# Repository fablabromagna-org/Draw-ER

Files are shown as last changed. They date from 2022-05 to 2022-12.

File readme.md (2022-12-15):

# Draw-ER
### da un'idea originale di [MakersBox](https://www.instructables.com/Arduino-Drawing-Robot/)
Un piccolo, lento ma economico robot disegnatore, autocostruibile da tutti e programmabile in Python per insegnare il coding in modo divertente.

# Eccolo
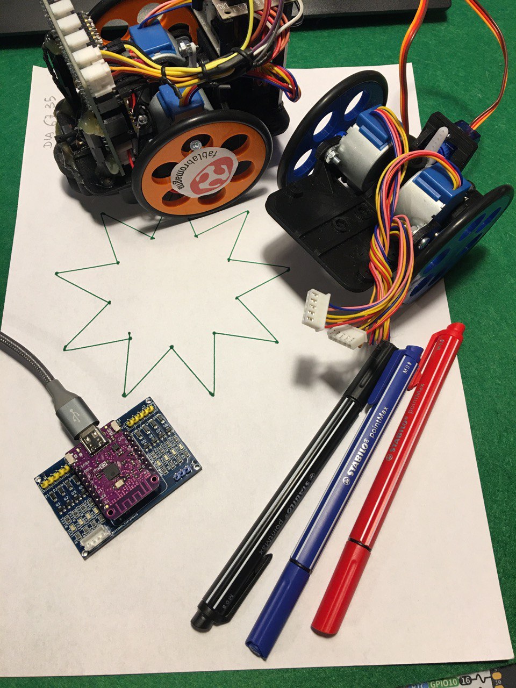
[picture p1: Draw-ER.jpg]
Draw-ER


## stampa la locandina da tenere in classe
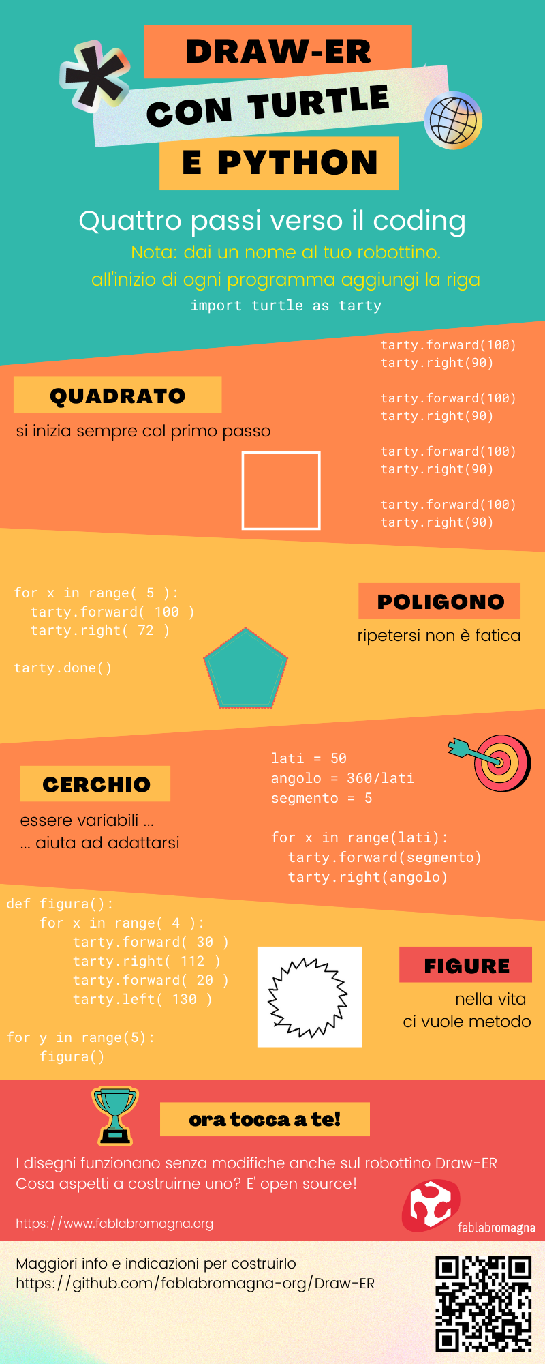
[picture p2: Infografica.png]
Locandina


## istruzioni per il montaggio

<a href="https://cutt.ly/montaggio-Draw-ER">link al documento GDocs</a>

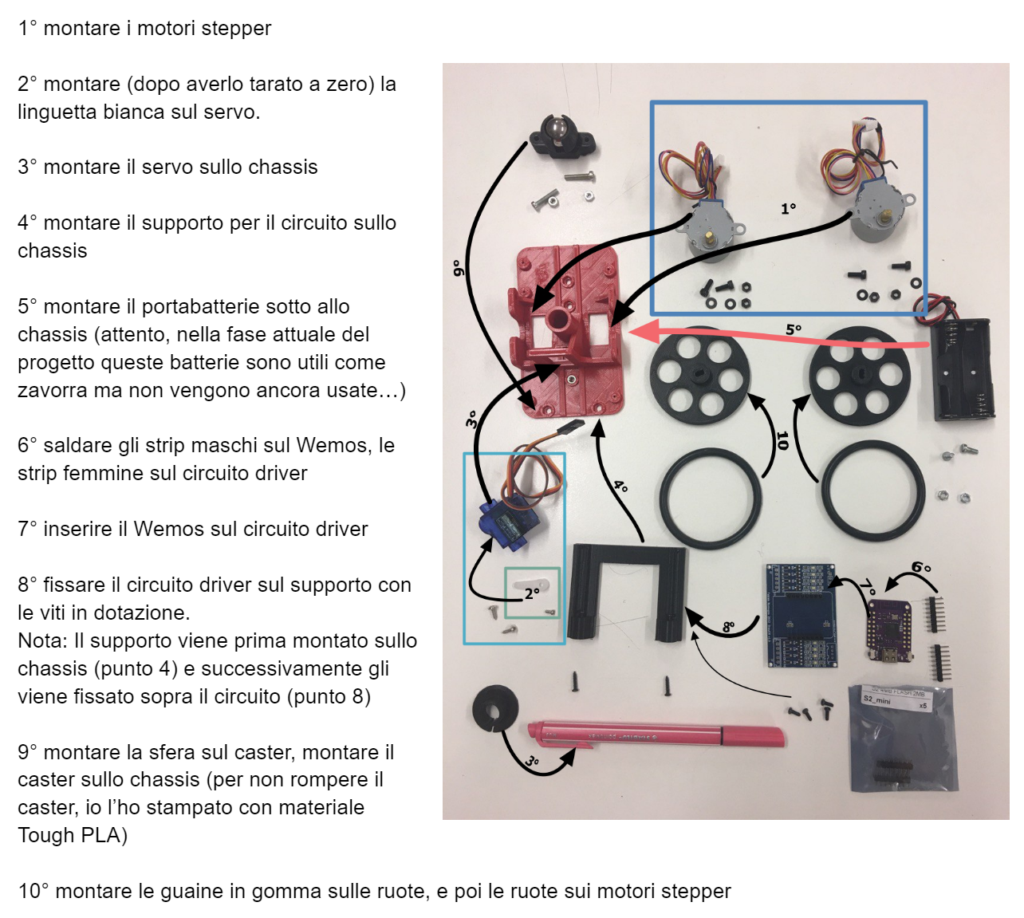
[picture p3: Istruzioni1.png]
Istruzioni


#### Ci serve un fornitore per queste viti... ci date una mano?
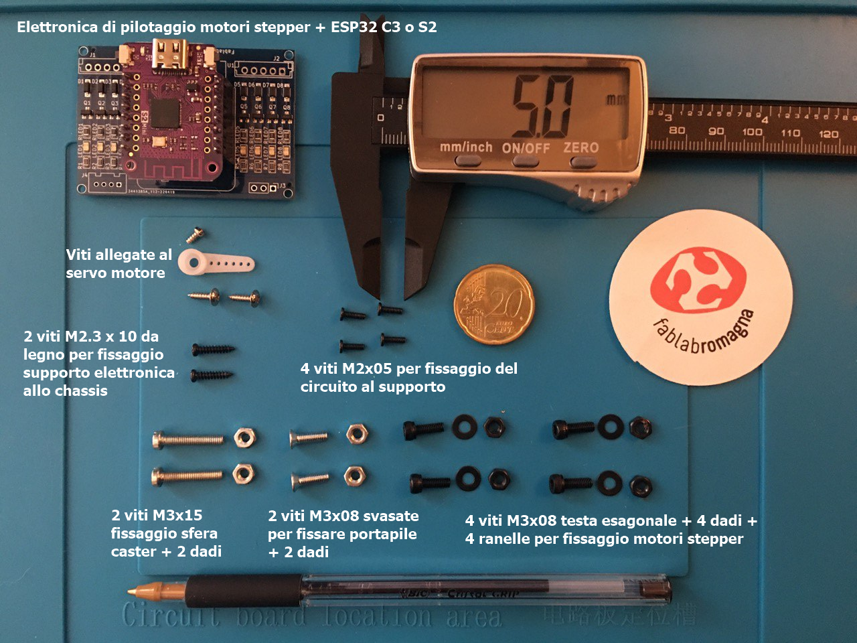
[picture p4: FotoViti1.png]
Viti


#### questa foto è utile per capire come sono montati i connettori
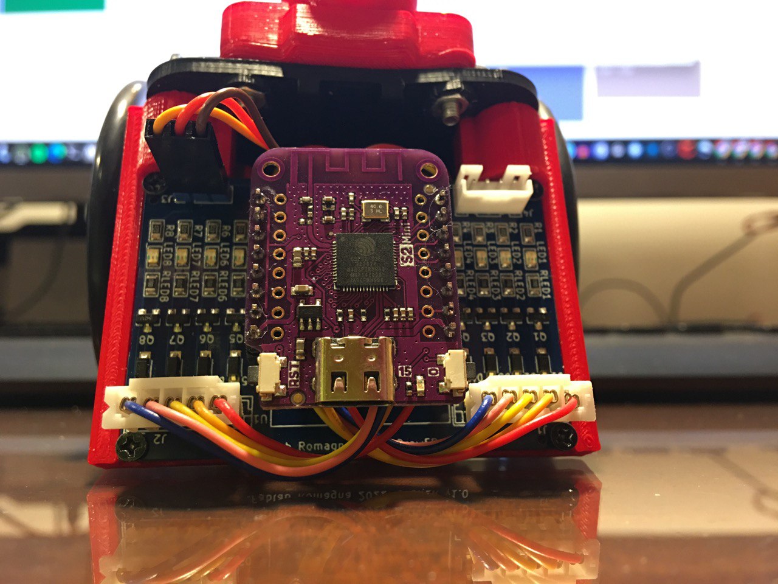
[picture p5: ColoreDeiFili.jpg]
Colore dei fili


## usa Kicad per modificare lo schema e il PCB

<a href="https://github.com/fablabromagna-org/Draw-ER/tree/master/File%20Kicad">Kicad</a>

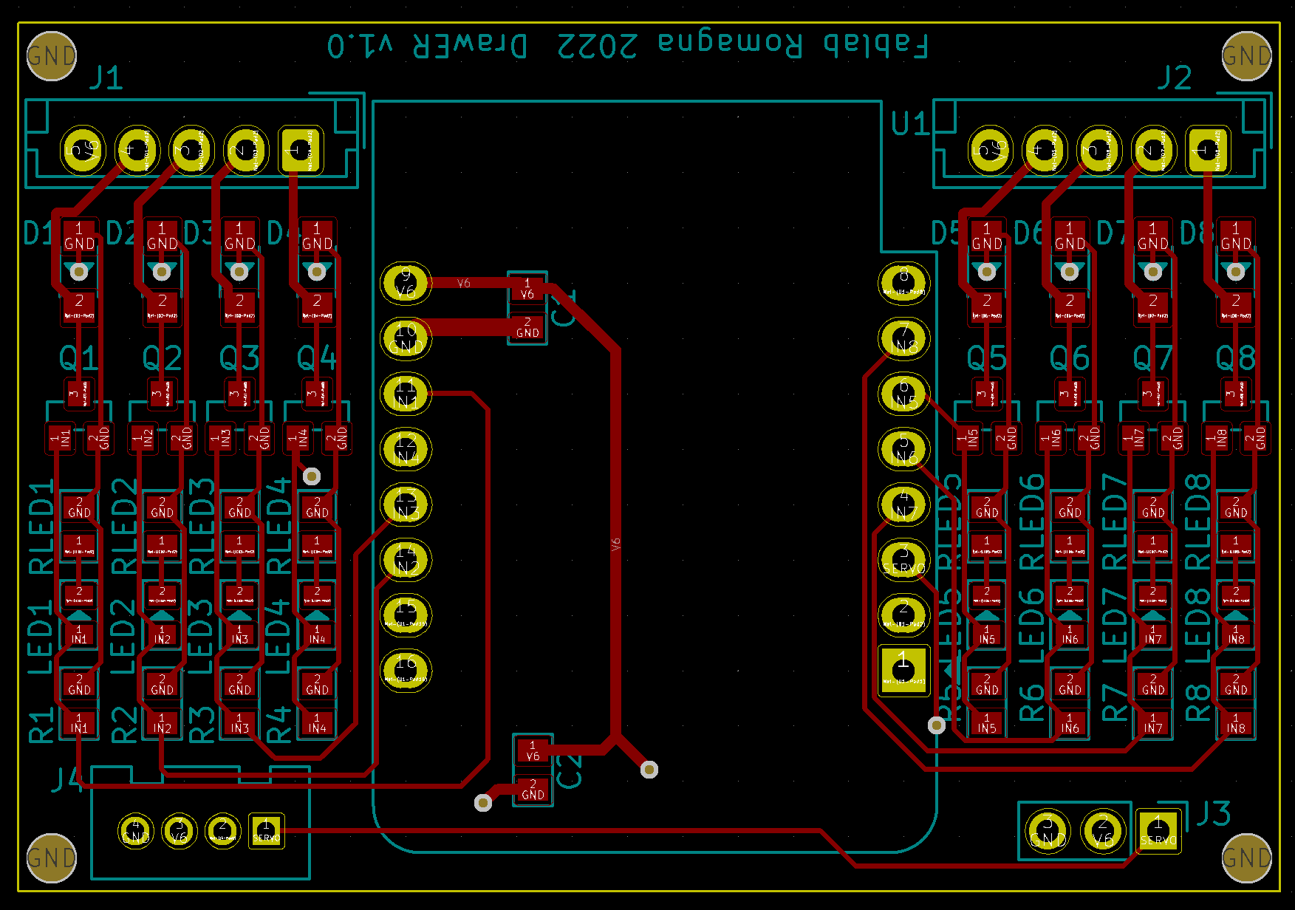
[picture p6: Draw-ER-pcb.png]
PCB


## dai un'occhiata allo schema
<a href="Schematic.pdf">Download PDF</a>

## dai un'occhiata anche al lavoro di Alessandro Capanna Kappa! che sta cercando in tutti i modi di togliere il filo!! :-)
https://github.com/1Kappa1/Draw-Er.utility.file

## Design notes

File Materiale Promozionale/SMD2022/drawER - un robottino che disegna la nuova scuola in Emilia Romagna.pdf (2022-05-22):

25/03/22, 17:28 | drawER - un robottino che disegna la nuova scuola in Emilia Romagna

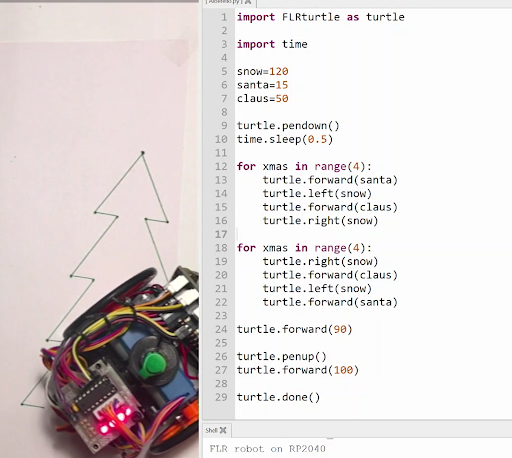
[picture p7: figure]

www.schoolmakerday.it/registrazione/candidatura/viewespol?id=a_491 | 1/3

Home registrazioni (/registrazione) (http://www.schoolmakerday.it/registrazione)
/ drawER - un robottino che disegna la nuova scuola in Emilia Romagna

Modifica (/registrazione/candidatura/espolupdate?id=a_491) (http://www.schoolmakerday.it/registrazione/candidatura/espolupdate?id=a_491)

# drawER - un robottino che disegna la nuova scuola in Emilia Romagna

Abbiamo realizzato un robottino per lo studio della geometria computazionale e del pensiero computazionale, usabile nelle scuole di primo grado ma realizzabile dai ragazzi e dalle ragazze delle superiori, per promuovere la collaborazione tra vari livelli e ordini di scuola.

Un'idea in parte ancora un po' sulla carta ma con un prototipo quasi funzionante in fase di sviluppo in due classi terze ITTS in ambito PCTO.
I progetti saranno pubblicati su github.com

# Chi siamo

## FabLab Romagna makerspace presso l'ITTS "Belluzzi - da Vinci"

Fablab

www.schoolmakerday.it/registrazione/candidatura/viewespol?id=a_491 | 2/3

Referente: Maurizio Conti

Presentazione del team da compilare

Sito web: (/registrazione/candidatura/viewespol?id=a_491) (http://www.schoolmakerday.it/registrazione/candidatura/viewespol?id=a_491)

Temi:
ambito Maker
Robotica
Stampa 3D
STEM
ambito Agenda2030
Istruzione di qualità
Parità di genere
ambito Azioni PNSD
Scenari innovativi per lo sviluppo di competenze digitali applicate
Portare il pensiero logico-computazionale a tutta la scuola primaria Aggiornare il curricolo di “Tecnologia” alla scuola secondaria di primo grado

# Ulteriori dati:

Dichiarazione liberatoria: si
Richiesta trasporto: si
Data di richiesta trasporto: 2022-03-25 17:25:49 Numero di partecipanti: 60
Torna all'elenco (/registrazione/candidatura/candidature) (http://www.schoolmakerday.it/registrazione/candidatura/candidature)

www.schoolmakerday.it/registrazione/candidatura/viewespol?id=a_491 | 3/3

© IIS Belluzzi-Fioravanti (http://www.belluzzifioravanti.it) / Servizio Marconi TSI USR-ER (http://serviziomarconi.w.istruzioneer.it/) 2016-2022. Powered by Yii Framework (http://www.yiiframework.com/). - Note relative a Privacy e Cookie (http://www.schoolmakerday.it/privacy-e-cookie/)

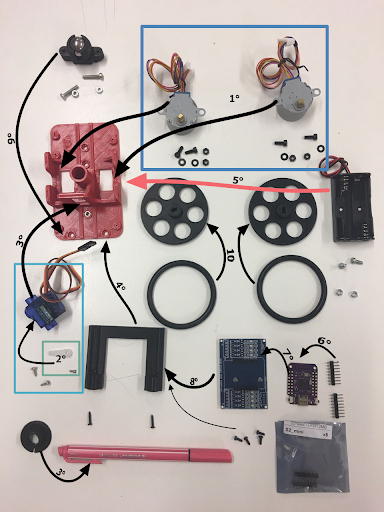
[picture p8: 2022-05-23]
Componenti.png

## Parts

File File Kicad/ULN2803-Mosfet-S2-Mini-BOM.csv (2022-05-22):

Comment | Designator | Footprint | LCSC
CERAMIC-10UF-10V-10%-X7R_0805_ | C1,C2 | OPL_Capacitor:C0805 | C126586
SMD-DIODE-SCHOTTKY-20V-1A_SOD-123_ | D1,D2,D3,D4,D5,D6,D7,D8 | OPL_Discrete:SOD-123 | C84354
Step Motor | J1,J2 | Connector_JST:JST_EH_B5B-EH-A_1x05_P2.50mm_Vertical
Conn_01x03_Male | J3 | Connector_PinHeader_2.54mm:PinHeader_1x03_P2.54mm_Vertical
GROVE-CONNECTOR-DIP_4P-2.0_ | J4 | OPL_Connector:HW4-2.0
SMD-LED-CLEAR-RED_0805_ | LED1,LED2,LED3,LED4,LED5,LED6,LED7,LED8 | OPL_Opto:LED-0805 | C2764885
SMD-MOSFET-N-CH-20V-2.1A-CJ2302_SOT-23_ | Q1,Q2,Q3,Q4,Q5,Q6,Q7,Q8 | OPL_Discrete:SOT-23 | C91104
SMD-RES-4.7K-5%-1_8W_0805_ | R1,R2,R3,R4,R5,R6,R7,R8 | OPL_Resistor:R0805 | C473295
SMD-RES-220R-5%-1_8W_0805_ | RLED1,RLED2,RLED3,RLED4,RLED5,RLED6,RLED7,RLED8 | OPL_Resistor:R0805 | C365277
WeMos_D1_mini | U1 | Module:WEMOS_D1_mini_light

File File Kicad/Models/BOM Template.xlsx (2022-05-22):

Designator | Manufacturer Part Number or Seeed SKU | Qty | Link
C1,C2,C3,C4,C5 | RHA0J471MCN1GS | 5 | https://www.digikey.com.cn/product-detail/zh/nichicon/RHA0J471MCN1GS/493-3771-1-ND/2209480
A1,A4 | RH0111-30002 | 2 | https://statics3.seeedstudio.com/images/opl/datasheet/318020010.pdf
D1 | CYBLE-014008-00 | 1 | https://www.digikey.com.cn/product-detail/zh/cypress-semiconductor-corp/CYBLE-014008-00/428-3600-1-ND/6052585

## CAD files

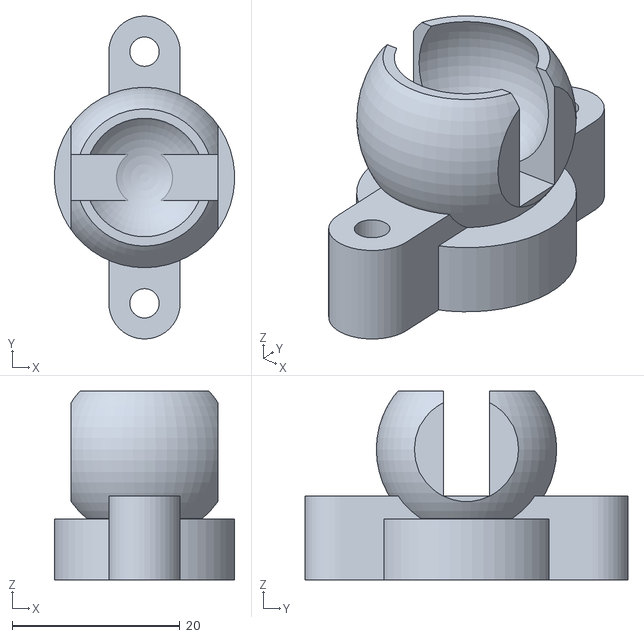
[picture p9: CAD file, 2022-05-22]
Cad3D/FLRCaster/FLRCaster.stl
21.5 x 38.5 x 22.5

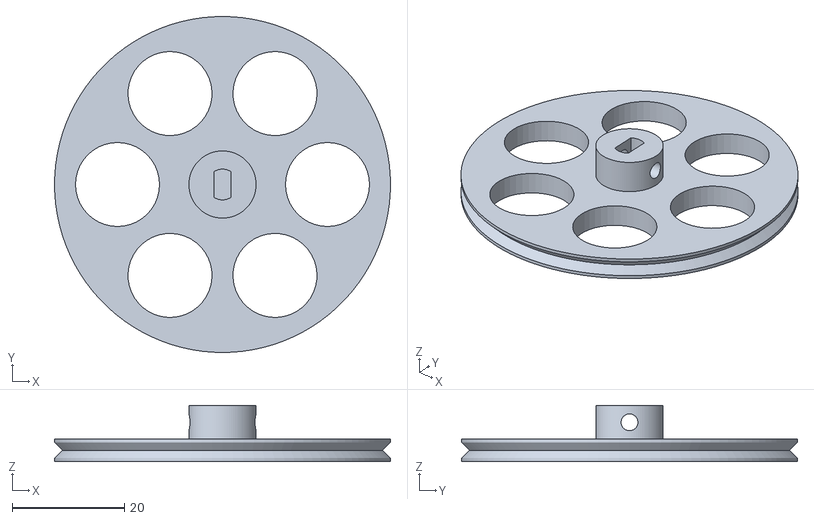
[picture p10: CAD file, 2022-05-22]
Cad3D/STL per SMD22/60mm_wheel_spoked.stl
60.0 x 60.0 x 10.0

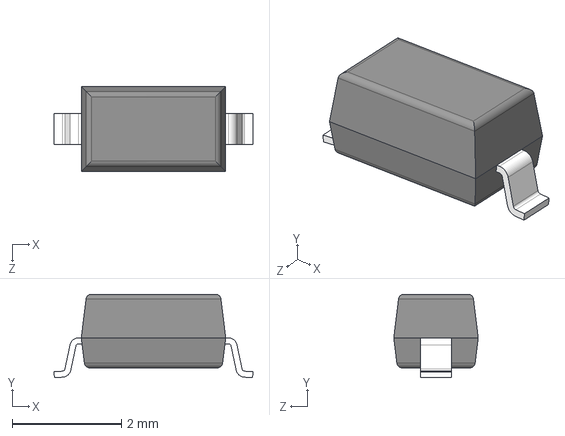
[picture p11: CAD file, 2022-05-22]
File Kicad/Models/B5819W-TP.step
3.65 x 1.53 x 1.55 mm

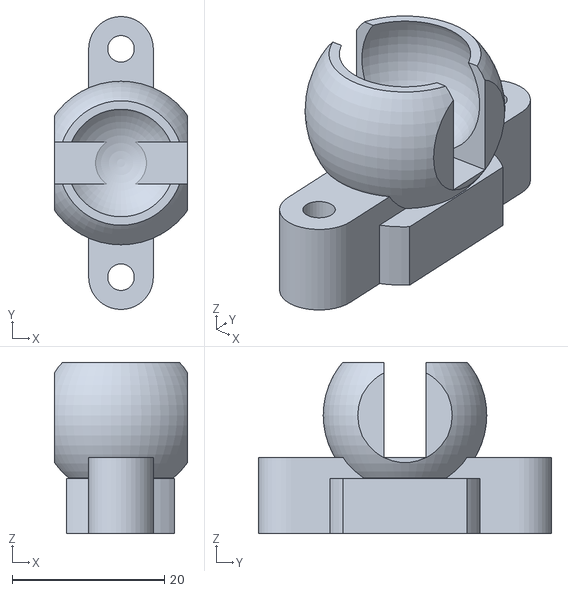
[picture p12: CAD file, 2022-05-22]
Cad3D/FLRCaster/FLRCaster V3 Smussato.stl
17.5 x 38.5 x 22.5

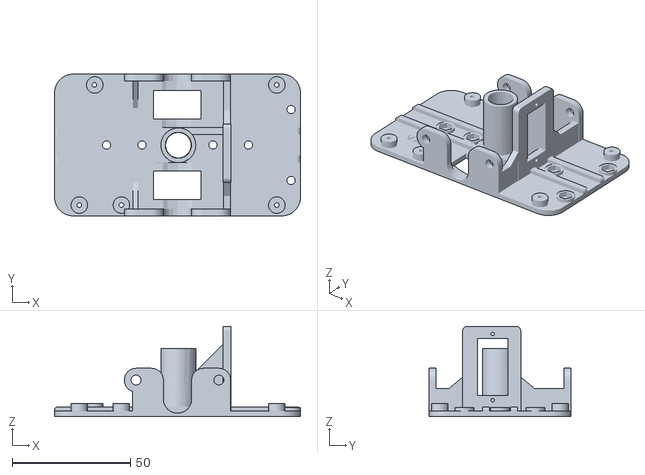
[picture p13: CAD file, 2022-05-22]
Cad3D/STL per SMD22/1x-Chassis v2.1.stl
104.0 x 60.0 x 38.3

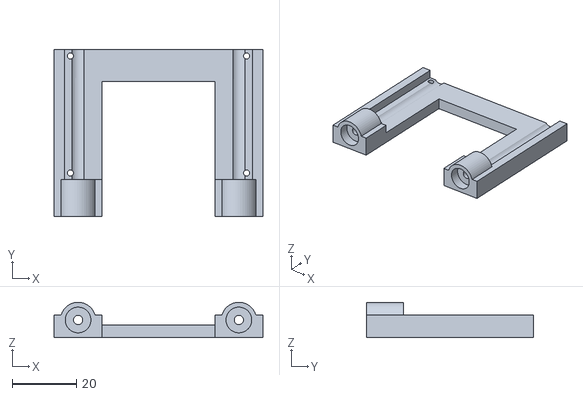
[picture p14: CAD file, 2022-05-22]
Cad3D/STL per SMD22/Supporto Wemos mini con fori.stl
65.0 x 52.0 x 11.0

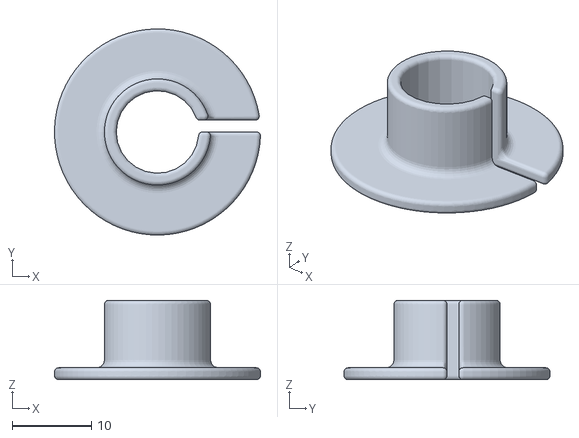
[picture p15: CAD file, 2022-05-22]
Cad3D/STL per SMD22/1xPenCollar10-4mm.stl
26.0 x 26.0 x 10.0

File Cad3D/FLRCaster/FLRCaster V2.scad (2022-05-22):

// Original: http://www.thingiverse.com/thing:8959/
// Marble Caster by HipsterLogic

// Modified by 648.ken@gmail.com
// MakersBox.blogspot.com

// Added tapper the top lip to keep it from snagging on things.
// Added recess for screw heads if baseThickness > 3mm
// Added pedistal base so you can adjust platform hieght.

// Modificato da maurizio.conti@ittsrimini.edu.it
// Alzata la quota di 7.3mm per portarlo alla pari dello chassis con ruote da 60mm



deckHeight = 18.5;    // from chassis bottom to ground, (must be at lease ballDiameter)
ballDiameter = 16.5;    // 7/16" ball bearing = 12.25mm, WAS 16.5  16mm = 5/8" ball bearing
ballTolerance = 0.25;  // play between ball and surface
wallThickness = 2.5;
gapWidth = ballDiameter / 3;
baseThickness = 10; // WAS 3
newQuota = 7.3;

//baseHeight = ballDiameter + wallThickness * 2;
pedistalWidth = ballDiameter + wallThickness * 2;

baseWidth = 30; // distance between mounting holes

M3holeDia = 3.5;
M3nutDia = 6.5;


echo(deckHeight);
baseHeight = deckHeight - ballDiameter / 2;
echo(baseHeight);

module mainShape(){

    // Alzata la quota di tutto l'assembly
    translate([0, 0, -newQuota]) {

        // mounting cross-piece
        translate([-baseWidth/2, -wallThickness - M3holeDia / 2, 0]) 
            cube([baseWidth, wallThickness * 2 + M3holeDia, baseThickness]);
        
        // bolt ends
        translate([baseWidth / 2, 0, 0]) 
            cylinder(baseThickness, M3holeDia / 2 + wallThickness, M3holeDia / 2 + wallThickness, $fn=40);
        translate([-baseWidth / 2, 0, 0]) 
            cylinder(baseThickness, M3holeDia / 2 + wallThickness, M3holeDia / 2 + wallThickness, $fn=40);

        // main cylindrical body
        translate([0, 0, 0])
            cylinder(baseHeight - 3, pedistalWidth / 2, pedistalWidth / 2, $fn=50);
    }
    
    difference(){
        // tapper shere at top
        translate([0, 0, baseHeight - 2])
            sphere(pedistalWidth / 2, $fn=50);
                
        // shave the top flat
        translate([0, 0, baseHeight + ballDiameter / 2 - ballDiameter / 5])
            cylinder(25, 25, 25, $fn=50);
        
        // shave the bottom	flat	
        translate([0, 0, -12])
            cylinder(12, 25, 25, $fn=50);
  
    };
}

module cutout(){
    
    // ball hole
	translate([0, 0, baseHeight + ballTolerance]) 
        sphere(ballDiameter / 2 + ballTolerance, $fn=50);
	
    // slot to remove ball
    slotOffset = ballDiameter / 2.5;  // distance below baseHeight to cut slot
    if (baseHeight - slotOffset > baseThickness){
        translate([-gapWidth / 2, -baseWidth / 2, baseHeight - slotOffset]) 
            cube([gapWidth, baseWidth, ballDiameter]);
        
        }
    else{ // don't cut into base
        translate([-gapWidth / 2, -baseWidth / 2, baseThickness-newQuota]) 
            cube([gapWidth, baseWidth, ballDiameter]);        
    }
    
    //trim sides
    translate([-25, ballDiameter / 2 + 0.5, 0]) 
            cube([50, ballDiameter, 50]);      

    translate([-25, -ballDiameter - 0.5, 0]) 
            cube([50, ballDiameter / 2, 50]);    

    if ((baseHeight - ballDiameter / 2) > baseThickness){
         // ball void to save material
        translate([0, 0, baseHeight - ballDiameter - 1]) 
            sphere(ballDiameter / 2, $fn=50);
    }

}

module mountingHoles(){

    // left m3 hole
	translate([baseWidth / 2, 0, -baseThickness ])
        cylinder(baseThickness + 3, M3holeDia / 2, M3holeDia / 2, $fn=30);

    // countersink
	//translate([baseWidth / 2, 0, 2]) 
    //rotate([0, 0, 30])
	//cylinder(baseThickness + 2, M3holeDia, //M3holeDia, $fn=6);

    // right m3 hole
	translate([-baseWidth / 2, 0, -baseThickness]) 
        cylinder(baseThickness + 3, M3holeDia / 2, M3holeDia/2, $fn=30);

    // countersink
	//translate([-baseWidth / 2, 0, 2]) 
    //rotate([0, 0, 30])
    //cylinder(baseThickness + 2, M3holeDia, M3holeDia, $fn=6);
}

rotate([0, 0, 90])

difference(){
	mainShape();
	cutout();
	mountingHoles();
}

// show ball?
//translate([0, 0, baseHeight]) 
//    sphere(ballDiameter/2, $fn=50);

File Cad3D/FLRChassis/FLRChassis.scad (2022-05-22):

$fn = 64;

include <FLRModule.scad>


baseThickness = 2.4;
cornerRounding = 8;
plateOffset = 0;    // shift entire plate on x axis
railOffset = 16;     // plate lenght - railLength
M3holeDia = 3.5;
M3nutDia = 6.5;
holeOffset = M3holeDia * 1.2;
batteryOffset = 15;
casterFromEdge = 4;   // from edge to CL of caster bolt holes
cassis_wid = 75; // 94 for full Raspberry Pi, 84 for A+ ?
cassis_len = 140;


penDiameter = 15.0;
penRadius = penDiameter / 2;
baseLen = 34.5;
baseWid = 20;

railWidth = 2;

cutout_len = 45;
cutout_wid = 15;

trinketX = -41.5;
trinketY = -50.8/2;
sensor_offset = 13;



difference(){
    
    union(){
        // cassis plate
        translate([-cassis_len / 2 - plateOffset, -cassis_wid / 2, 0])
        roundedCube(cassis_len, cassis_wid, baseThickness, cornerRounding);
        

        // rails
        rail_offset = 5.5;
        translate([-cassis_len / 2 - plateOffset, 
                   +rail_offset+railWidth, baseThickness / 2])
            rotate([90, 0, 0])    
            roundedCube(cassis_len/2-8, 3.0, railWidth, 1);

        translate([-cassis_len / 2 - plateOffset, 
                   - rail_offset, baseThickness / 2])
            rotate([90, 0, 0])    
            roundedCube(cassis_len/2-8, 3.0, railWidth, 1); 

        translate([8, 
                   - rail_offset+railWidth -2, baseThickness / 2])
            rotate([90, 0, 0])    
            roundedCube(cassis_len/2-8, 3.0, railWidth, 1);

        translate([8, 
                   + rail_offset +2, baseThickness / 2])
            rotate([90, 0, 0])    
            roundedCube(cassis_len/2-8, 3.0, railWidth, 1); 


        
        //battery standoffs
        translate([batteryOffset, 0, baseThickness - 1])
        cylinder(baseThickness, standoffDia + 1, standoffDia + 1);  
        translate([batteryOffset + 15, 0, baseThickness - 1])
        cylinder(baseThickness, standoffDia + 1, standoffDia + 1);
        //translate([batteryOffset + 30, 0, baseThickness - 1])
        //cylinder(baseThickness, d=standoffDia + 1, d=standoffDia + 1);   

        //translate([-batteryOffset, 0, baseThickness - 1])
        //cylinder(baseThickness, d=standoffDia + 1, d=standoffDia + 1);  
        translate([-batteryOffset - 0, 0, baseThickness - 1])
        cylinder(baseThickness, standoffDia + 1, standoffDia + 1);
        translate([-batteryOffset - 15, 0, baseThickness - 1])
        cylinder(baseThickness, standoffDia + 1, standoffDia + 1);        

        // caster standoffs
        translate([cassis_len / 2 - casterFromEdge - plateOffset, -15, baseThickness -1])
        cylinder(baseThickness, standoffDia + 1, standoffDia + 1);  
        translate([cassis_len / 2 - casterFromEdge - plateOffset, 15, baseThickness -1])
        cylinder(baseThickness, standoffDia + 1, standoffDia + 1); 

        // trinket standoffs
        translate([trinketX, trinketY, 0])
        cylinder(standoffThickness, standoffDia / 2, standoffDia / 2);
        
        translate([trinketX + 17.8, trinketY, 0])
        cylinder(standoffThickness, standoffDia / 2, standoffDia / 2);        

        translate([trinketX + 17.8, trinketY + 50.8, 0])
        cylinder(standoffThickness, standoffDia / 2, standoffDia / 2);

        translate([trinketX, trinketY + 50.8, 0])
        cylinder(standoffThickness, standoffDia / 2, standoffDia / 2);        

        // nose standoffs
        translate([cassis_len/2 - 14, trinketY, 0])
        cylinder(standoffThickness, standoffDia / 2, standoffDia / 2);

        translate([cassis_len/2 - 14, trinketY + 50.8, 0])
        cylinder(standoffThickness, standoffDia / 2, standoffDia / 2); 

        
    }

    // center pen hole
    cylinder(baseThickness * 2, penRadius, penRadius);

   
    // caster holes
    translate([cassis_len / 2 - casterFromEdge - plateOffset, -15, 0])
    cylinder(baseThickness*2, M3holeDia, M3holeDia);     
    translate([cassis_len / 2 - casterFromEdge - plateOffset, 15, 0])
    cylinder(baseThickness*2, M3holeDia, M3holeDia);    

    // caster nut nolders
    translate([cassis_len / 2 - casterFromEdge - plateOffset, -15, baseThickness - 1])
    cylinder(baseThickness, M3nutDia, M3nutDia, $fn=6);
    translate([cassis_len / 2 - casterFromEdge - plateOffset, 15, baseThickness - 1])
    cylinder(baseThickness, M3nutDia, M3nutDia, $fn=6);

 
    // battery holes
    translate([batteryOffset, 0, 0])
    cylinder(baseThickness, M3holeDia, M3holeDia);  
    translate([batteryOffset + 15, 0, 0])
    cylinder(baseThickness, M3holeDia, M3holeDia);
    
    translate([-batteryOffset - 0, 0, 0])
    cylinder(baseThickness, M3holeDia, M3holeDia);
    translate([-batteryOffset - 15, 0, 0])
    cylinder(baseThickness, M3holeDia, M3holeDia); 

    // battery nut nolders
    translate([batteryOffset, 0, baseThickness - 1])
    cylinder(baseThickness, M3nutDia, M3nutDia, $fn=6);
    translate([batteryOffset + 15, 0, baseThickness - 1])
    cylinder(baseThickness, M3nutDia, M3nutDia, $fn=6);

    translate([-batteryOffset - 0, 0, baseThickness - 1])
    cylinder(baseThickness, M3nutDia, M3nutDia, $fn=6);
    translate([-batteryOffset - 15, 0, baseThickness - 1])
    cylinder(baseThickness, M3nutDia, M3nutDia, $fn=6);

    // trinket holes
    translate([trinketX, trinketY, 0])
    cylinder(standoffThickness * 2, standoffHoleDia / 2, standoffHoleDia / 2);

    translate([trinketX + 17.8, trinketY, 0])
    cylinder(standoffThickness * 2, standoffHoleDia / 2, standoffHoleDia / 2);

    translate([trinketX, trinketY + 50.8, 0])
    cylinder(standoffThickness * 2, standoffHoleDia / 2, standoffHoleDia / 2);

    translate([trinketX + 17.8, trinketY + 50.8, 0])
    cylinder(standoffThickness * 2, standoffHoleDia / 2, standoffHoleDia / 2);

    // nose standoff holees
    translate([cassis_len/2-14, trinketY, 0])
    cylinder(standoffThickness * 2, standoffHoleDia / 2, standoffHoleDia / 2);

    translate([cassis_len/2 -14, trinketY + 50.8, 0])
    cylinder(standoffThickness * 2, standoffHoleDia / 2, standoffHoleDia / 2);

 
}


standoffDia = 7;
standoffThickness = 5.5;
standoffHoleDia = 2;

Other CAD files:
Cad3D/STL per SMD22/Ruota60 con foro allargato e nuts più piccole.stl
Cad3D/FLRCaster/FLRCaster V3 Smussato.scad
Cad3D/FLRChassis/FLRModule.scad

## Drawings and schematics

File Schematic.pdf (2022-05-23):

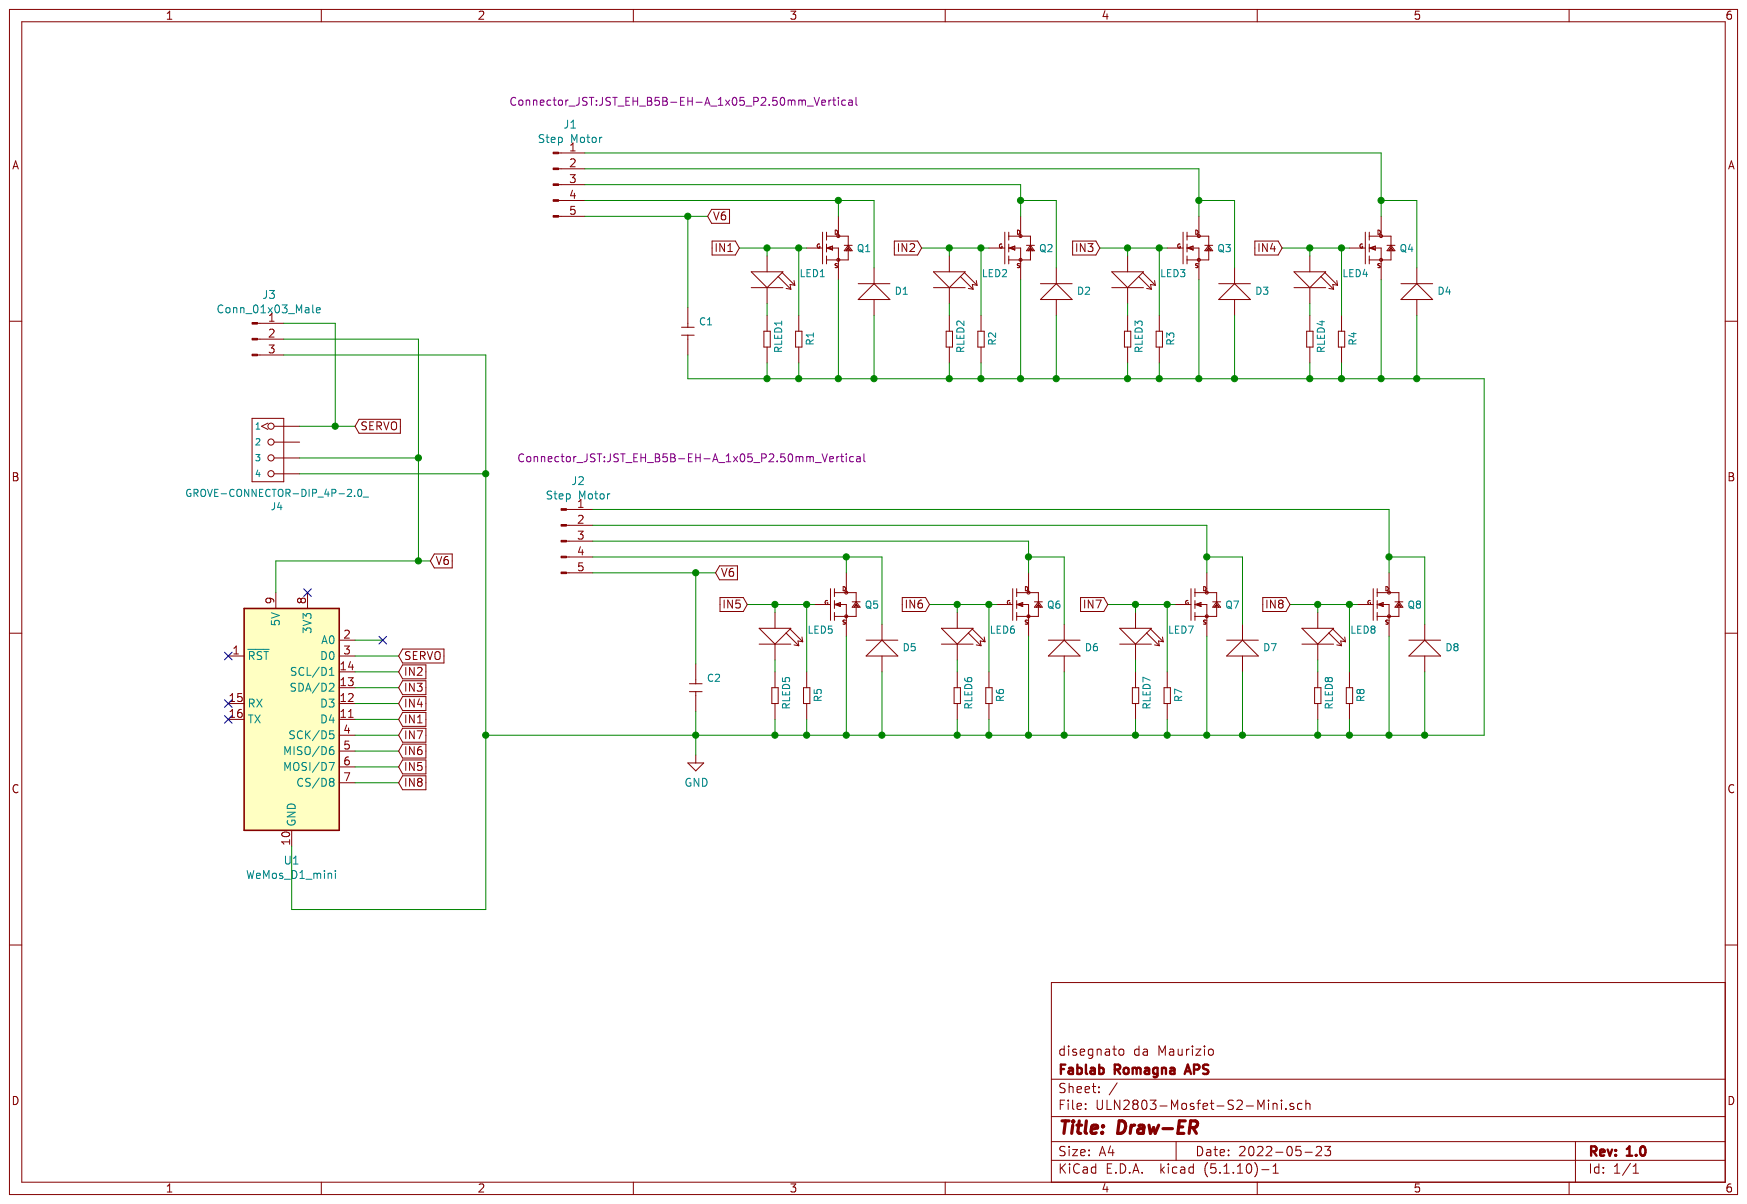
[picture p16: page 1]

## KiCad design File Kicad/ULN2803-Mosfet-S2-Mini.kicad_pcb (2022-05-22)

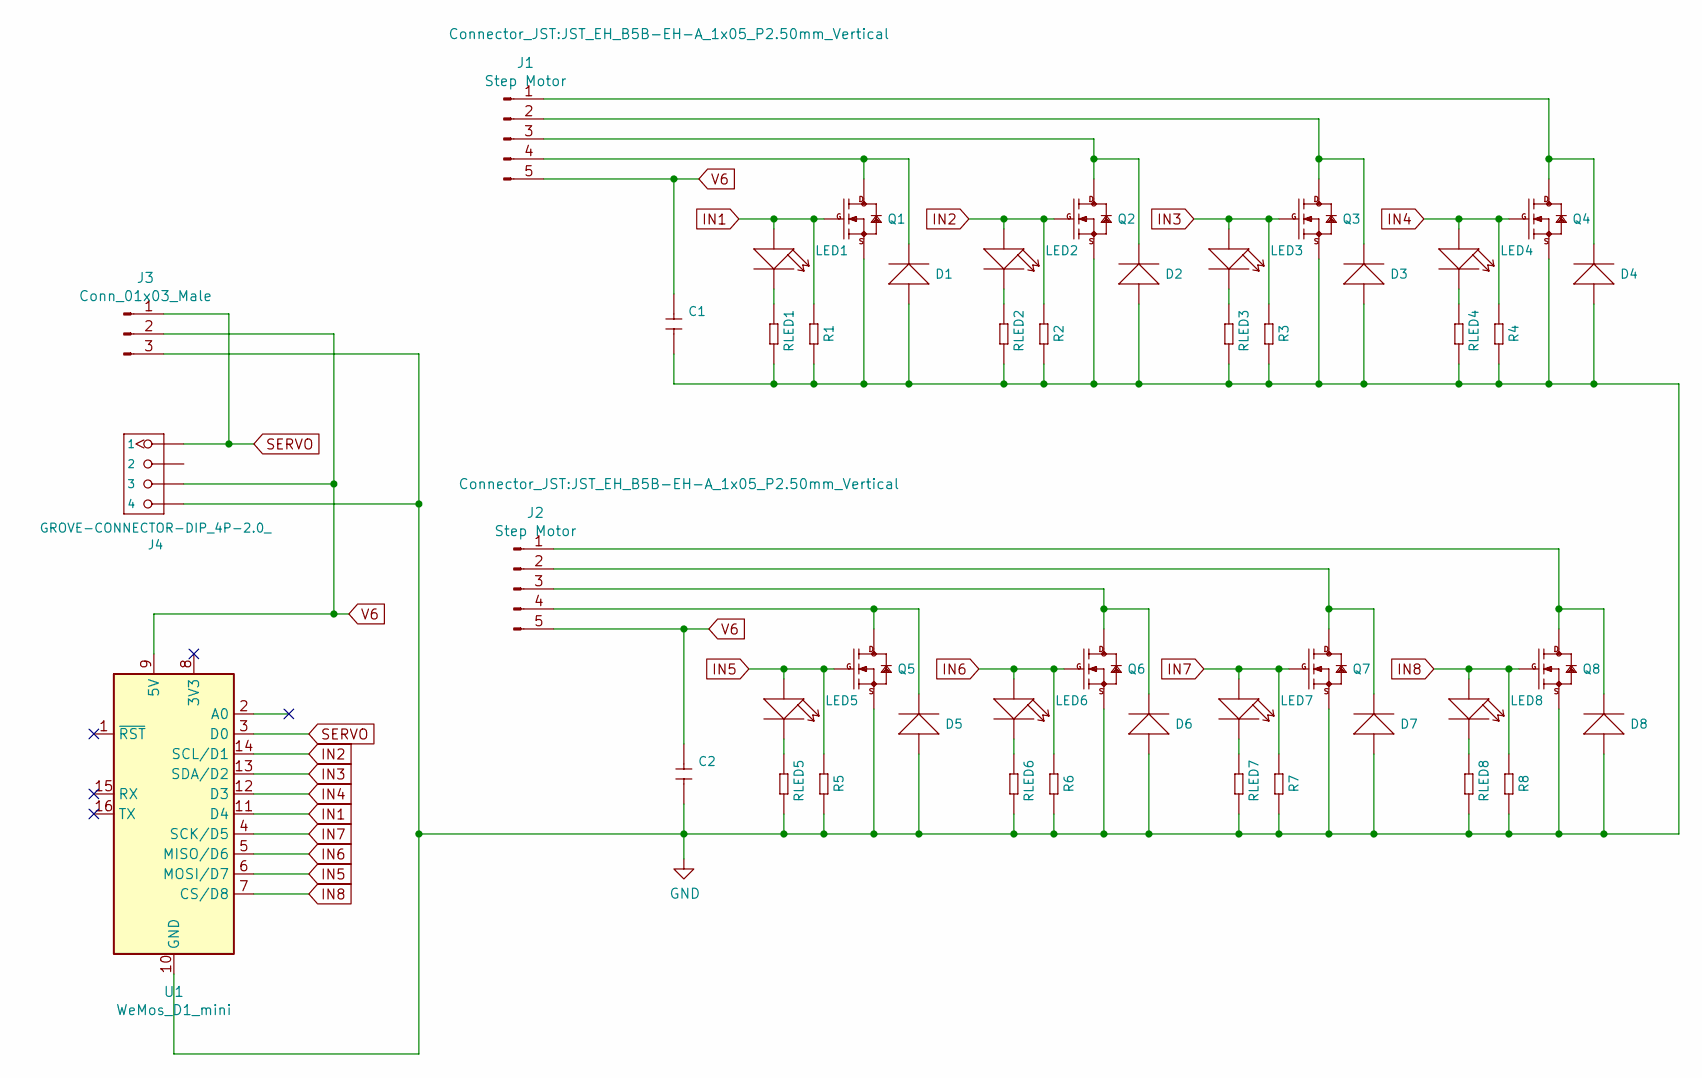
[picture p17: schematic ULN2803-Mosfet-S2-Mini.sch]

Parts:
C1, C2: CERAMIC-10UF-10V-10%-X7R_0805_; C0805; MPN CC0805ZKY5V6BB106; LCSC C126586
D1, D2, D3, D4, D5, D6, D7, D8: SMD-DIODE-SCHOTTKY-20V-1A_SOD-123_; SOD-123; MPN B5819W; LCSC C84354
J1, J2: Step Motor; JST_EH_B5B-EH-A_1x05_P2.50mm_Vertical
J3: Conn_01x03_Male; PinHeader_1x03_P2.54mm_Vertical
J4: GROVE-CONNECTOR-DIP_4P-2.0_; HW4-2.0
LED1, LED2, LED3, LED4, LED5, LED6, LED7, LED8: SMD-LED-CLEAR-RED_0805_; LED-0805; MPN 17-215SURC_S530-A2_TR8; LCSC C2764885
Q1, Q2, Q3, Q4, Q5, Q6, Q7, Q8: SMD-MOSFET-N-CH-20V-2.1A-CJ2302_SOT-23_; SOT-23; MPN CJ2302; LCSC C91104
R1, R2, R3, R4, R5, R6, R7, R8: SMD-RES-4.7K-5%-1_8W_0805_; R0805; MPN RC0805JR-074K7L; LCSC C473295
RLED1, RLED2, RLED3, RLED4, RLED5, RLED6, RLED7, RLED8: SMD-RES-220R-5%-1_8W_0805_; R0805; MPN RC0805JR-07220RL; LCSC C365277
U1: WeMos_D1_mini; WEMOS_D1_mini_light

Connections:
GND: C1.2, C2.2, D1.1 (+), D2.1 (+), D3.1 (+), D4.1 (+), D5.1 (+), D6.1 (+), D7.1 (+), D8.1 (+), J3.3, J4.4, Q1.2 (S), Q2.2 (S), Q3.2 (S), Q4.2 (S), Q5.2 (S), Q6.2 (S), Q7.2 (S), Q8.2 (S), R1.2, R2.2, R3.2, R4.2, R5.2, R6.2, R7.2, R8.2, RLED1.2, RLED2.2, RLED3.2, RLED4.2, RLED5.2, RLED6.2, RLED7.2, RLED8.2, U1.10 (GND)
IN1: LED1.1 (+), Q1.1 (G), R1.1, U1.11 (D4)
IN2: LED2.1 (+), Q2.1 (G), R2.1, U1.14 (SCL/D1)
IN3: LED3.1 (+), Q3.1 (G), R3.1, U1.13 (SDA/D2)
IN4: LED4.1 (+), Q4.1 (G), R4.1, U1.12 (D3)
IN5: LED5.1 (+), Q5.1 (G), R5.1, U1.6 (MOSI/D7)
IN6: LED6.1 (+), Q6.1 (G), R6.1, U1.5 (MISO/D6)
IN7: LED7.1 (+), Q7.1 (G), R7.1, U1.4 (SCK/D5)
IN8: LED8.1 (+), Q8.1 (G), R8.1, U1.7 (CS/D8)
unnamed: D1.2 (-), J1.4, Q1.3 (D)
unnamed: D2.2 (-), J1.3, Q2.3 (D)
unnamed: D3.2 (-), J1.2, Q3.3 (D)
unnamed: D4.2 (-), J1.1, Q4.3 (D)
unnamed: D5.2 (-), J2.4, Q5.3 (D)
unnamed: D6.2 (-), J2.3, Q6.3 (D)
unnamed: D7.2 (-), J2.2, Q7.3 (D)
unnamed: D8.2 (-), J2.1, Q8.3 (D)
unnamed: LED1.2 (-), RLED1.1
unnamed: LED2.2 (-), RLED2.1
unnamed: LED3.2 (-), RLED3.1
unnamed: LED4.2 (-), RLED4.1
unnamed: LED5.2 (-), RLED5.1
unnamed: LED6.2 (-), RLED6.1
unnamed: LED7.2 (-), RLED7.1
unnamed: LED8.2 (-), RLED8.1
SERVO: J3.1, J4.1, U1.3 (D0)
V6: C1.1, C2.1, J1.5, J2.5, J3.2, J4.3, U1.9 (5V)

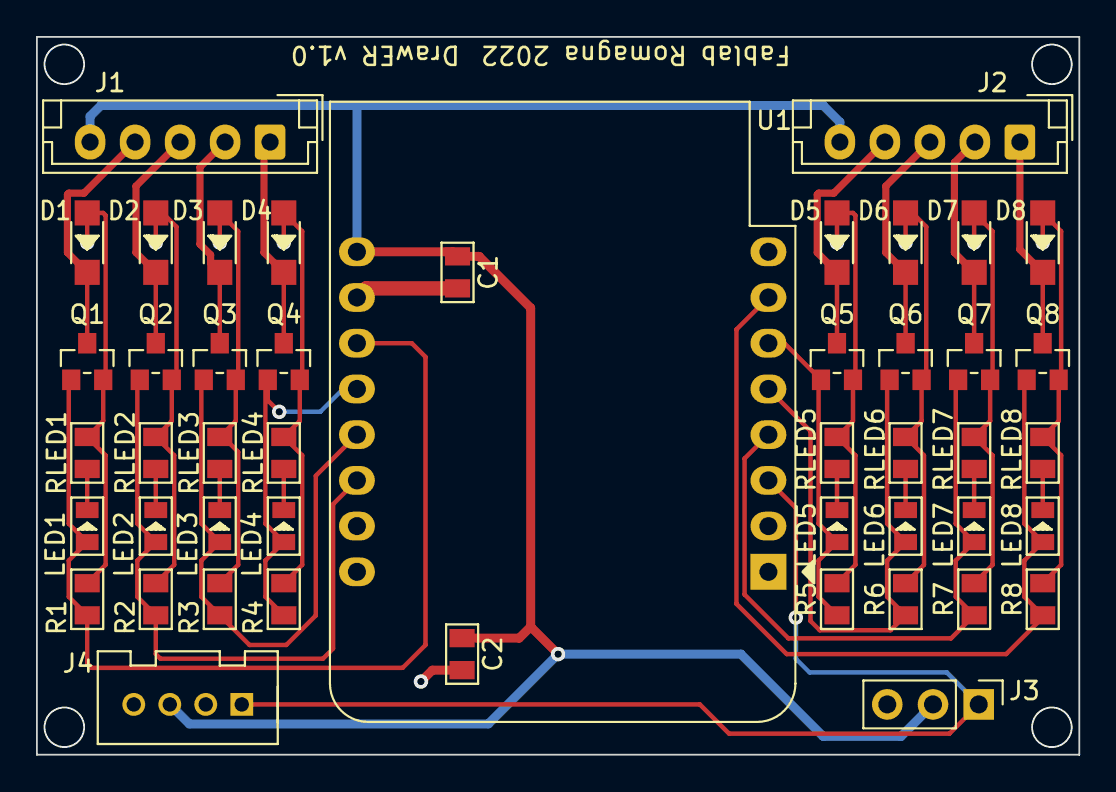
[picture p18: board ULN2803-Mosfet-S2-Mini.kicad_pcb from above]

Board: 2 copper layers, 57.9 x 39.9 mm, 47 parts (0 on the bottom side), 27 nets.

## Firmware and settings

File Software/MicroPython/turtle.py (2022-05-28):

# Libreria Turtle per Micro Python
# Maurizio Conti - Fablab Romagna 2022


import sys
import math
import time
import machine
import calibration

#import digitalio
#from analogio import AnalogIn

# Servo per Circuit Python
#import pulseio
#import adafruit_motor.servo
#import pwmio
#pwm = pulseio.PWMOut(board.GP20, frequency=50)
#pwm = pwmio.PWMOut(board.GP20, duty_cycle=2 ** 15, frequency=50)
#servo = adafruit_motor.servo.Servo( pwm,  min_pulse=calibration.min_pulse, max_pulse=calibration.max_pulse )

# Servo per Micro python ESP32 S2
#pinServo = machine.Pin(5, machine.Pin.OUT)
#servo = machine.PWM(pinServo, freq=42)

# Servo per Micro python ESP32 C3
pinServo = machine.Pin(1, machine.Pin.OUT)
servo = machine.PWM(pinServo, freq=42)

DEBUG = True

# [blu-rosa-giallo-arancio]
# Versione Raspberry Pi Pico
#Lstep0 = machine.Pin(2, machine.Pin.OUT) #Q4
#Lstep1 = machine.Pin(4, machine.Pin.OUT) #Q3
#Lstep2 = machine.Pin(6, machine.Pin.OUT) #Q2
#Lstep3 = machine.Pin(8, machine.Pin.OUT) #Q1

#Rstep0 = machine.Pin(3, machine.Pin.OUT) #Q8
#Rstep1 = machine.Pin(5, machine.Pin.OUT) #Q7
#Rstep2 = machine.Pin(7, machine.Pin.OUT) #Q6
#Rstep3 = machine.Pin(9, machine.Pin.OUT) #Q5


# [blu-rosa-giallo-arancio]
# Versione ESP8266 su Wemos D1 R2
#Lstep0 = machine.Pin(16, machine.Pin.OUT)
#Lstep1 = machine.Pin(5, machine.Pin.OUT)
#Lstep2 = machine.Pin(4, machine.Pin.OUT)
#Lstep3 = machine.Pin(0, machine.Pin.OUT)

#Rstep0 = machine.Pin(2, machine.Pin.OUT)
#Rstep1 = machine.Pin(14, machine.Pin.OUT)
#Rstep2 = machine.Pin(12, machine.Pin.OUT)
#Rstep3 = machine.Pin(13, machine.Pin.OUT)

# [blu-rosa-giallo-arancio]
# Versione ESP32 S2 su Wemos S2 mini
#Lstep0 = machine.Pin(18, machine.Pin.OUT) #Q4
#Lstep1 = machine.Pin(33, machine.Pin.OUT) #Q3
#Lstep2 = machine.Pin(35, machine.Pin.OUT) #Q2
#Lstep3 = machine.Pin(16, machine.Pin.OUT) #Q1

#Rstep0 = machine.Pin(12, machine.Pin.OUT) #Q8
#Rstep1 = machine.Pin(7, machine.Pin.OUT) #Q7
#Rstep2 = machine.Pin(9, machine.Pin.OUT) #Q6
#Rstep3 = machine.Pin(11, machine.Pin.OUT) #Q5

# [blu-rosa-giallo-arancio]
# Versione Wemos C3 mini
Lstep0 = machine.Pin(7, machine.Pin.OUT)  #Q4
Lstep1 = machine.Pin(8, machine.Pin.OUT)  #Q3
Lstep2 = machine.Pin(10, machine.Pin.OUT) #Q2
Lstep3 = machine.Pin(6, machine.Pin.OUT)  #Q1

Rstep0 = machine.Pin(5, machine.Pin.OUT)  #Q8
Rstep1 = machine.Pin(2, machine.Pin.OUT)  #Q7
Rstep2 = machine.Pin(3, machine.Pin.OUT)  #Q6
Rstep3 = machine.Pin(4, machine.Pin.OUT)  #Q5

# put connections in array to make life easier
R_stepper = [Rstep0, Rstep1, Rstep2, Rstep3]
L_stepper = [Lstep0, Lstep1, Lstep2, Lstep3]

#for wire in L_stepper:
#    wire.direction = digitalio.Direction.OUTPUT

#for wire in R_stepper:
#    wire.direction = digitalio.Direction.OUTPUT

# stepper patterns
patterns = [[1, 1, 0, 0], [0, 1, 1, 0], [0, 0, 1, 1], [1, 0, 0, 1]]

_x = 0
_y = 0
_heading = 0
frac_error = 0
spacer = ''


def setDebug(val):
    global DEBUG
    DEBUG = val

def step(distance):
    steps = distance * calibration.steps_rev/(calibration.wheel_dia * math.pi)
    frac = steps-int(steps)
    if frac > 0.5:
        return int(steps + 1), 1 - frac
    else:
        return int(steps), -frac

def forward(distance):
    global _x, _y, _heading
    steps, frac = step(distance)
    
    if DEBUG:
        print("dist %s, steps %s, frac %s" % (distance, steps, frac))

    for x in range(steps):
        for pattern in range(len(patterns)):
            for bit in range(len(patterns[pattern])):  # fwd_mask[num]:
                if not calibration.invert_direction:
                    L_stepper[bit].value(patterns[pattern][bit])
                    R_stepper[bit].value(patterns[::-1][pattern][bit])
                else:
                    R_stepper[bit].value(patterns[pattern][bit])
                    L_stepper[bit].value(patterns[::-1][pattern][bit])
            time.sleep(calibration.delay_time/1000)

    # new point
    deltax = distance * math.cos(math.radians(_heading))
    deltay = distance * math.sin(math.radians(_heading))
    _x = _x + deltax
    _y = _y + deltay


def backward(distance):
    global _x, _y, _heading
    steps, frac = step(distance)

    if DEBUG:
        print("dist %s, steps %s, frac %s" % (distance, steps, frac))

    for x in range(steps):
        for pattern in range(len(patterns)):
            for bit in range(len(patterns[pattern])):  # fwd_mask[num]:
                if not calibration.invert_direction:
                    R_stepper[bit].value = patterns[pattern][bit]
                    L_stepper[bit].value = patterns[::-1][pattern][bit]
                else:
                    L_stepper[bit].value = patterns[pattern][bit]
                    R_stepper[bit].value = patterns[::-1][pattern][bit]
            time.sleep(calibration.delay_time/1000)

    # new point
    deltax = distance * math.cos(math.radians(_heading - 180))
    deltay = distance * math.sin(math.radians(_heading - 180))
    _x = _x + deltax
    _y = _y + deltay


def left(degrees):
    global _x, _y, _heading, frac_error
    
    if (degrees < 0):
        right(-degrees)
        
    else:
    
        rotation = degrees / 360.0
        distance = calibration.wheel_base * math.pi * rotation
        steps, frac = step(distance)
        frac_error += frac

        if DEBUG:
            print("dist %s, steps %s, frac %s" % (distance, steps, frac))

        for x in range(steps):
            for pattern in range(len(patterns)):
                for bit in range(len(patterns[pattern])):  # fwd_mask[num]:
                    if not calibration.invert_direction:
                        R_stepper[bit].value(patterns[pattern][bit])
                        L_stepper[bit].value(patterns[pattern][bit])
                    else:
                        R_stepper[bit].value(patterns[::-1][pattern][bit])
                        L_stepper[bit].value(patterns[::-1][pattern][bit])
                time.sleep(calibration.delay_time/1000)
        
        _heading = _heading + degrees
        
        while _heading > 360:
            _heading = _heading - 360
        
        if DEBUG:
            print("dist %s, steps %s, frac %s, frac err %s" % (distance, steps, frac, frac_error))
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

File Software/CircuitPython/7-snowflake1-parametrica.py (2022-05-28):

#
# Coding Explosion!
# 10-11-2021
#
# Elisabetta Siboni e Maurizio Conti
# Servizio Marconi - USR-ER 2021
#
import turtle

primoSegmento = 12
segmento = 10
segmento_indietro = 3*primoSegmento

turtle.pendown()

for x in range(8):
 
    for y in range(3):
        turtle.forward(primoSegmento)
        turtle.right(45)
        turtle.forward(segmento)
        turtle.penup()
        turtle.backward(segmento)
        turtle.pendown()
        turtle.left(90)
        turtle.forward(segmento)
        turtle.penup()
        turtle.backward(segmento)
        turtle.pendown()
        turtle.right(45)

    turtle.backward(segmento_indietro)
    turtle.right(45)

turtle.done()

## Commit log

2022-05-22 Primo commit
    [60mm_wheel_spoked.stl]
2022-12-15 Link al lavoro di 1kappa1 su BLE
